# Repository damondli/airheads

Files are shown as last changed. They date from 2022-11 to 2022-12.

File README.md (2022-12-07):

#  ME507 Airheads Glider Project

<div class="title_screenshot">

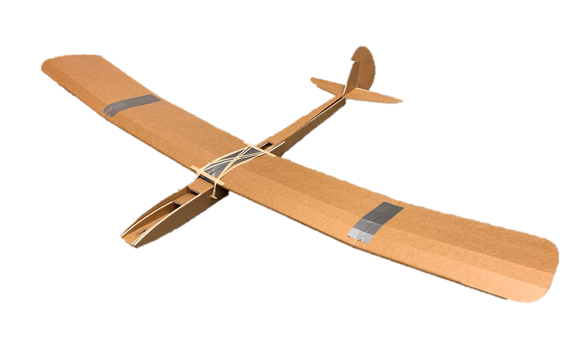
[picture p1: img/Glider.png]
Figure 1. Glider


</div>

This repository documents the development of a flight stabilization system for a glider.
To access our written report for this project, click [here](Airheads_Term_Project_Report_ME507.pdf).

## Background

This is a term project for Cal Poly's ME507 class. The scope of our project consists of:

- Background/Research and Identifying Specifications
- Hardware Design
- Custom PCB Design
- Software Design
- Internet of Things Implementation
- Proper Documentation 

## Hardware Design

To make this project more challenging and more fitting for ME507, we decided to use micro servo body DC motors instead of servos. To implement some form of feedback for the position of the motors, a motor mount was designed to couple a potentiometer to the shaft of the motor.

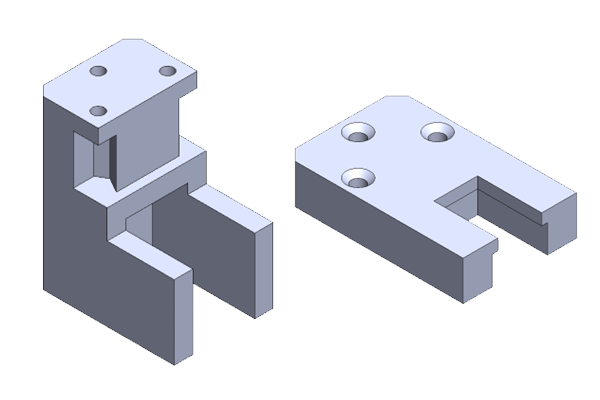
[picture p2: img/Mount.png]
Figure 2. Custom Motor Bracket


## Custom PCB Design

Our custom PCB is designed to fit on an ESP32 feather board.

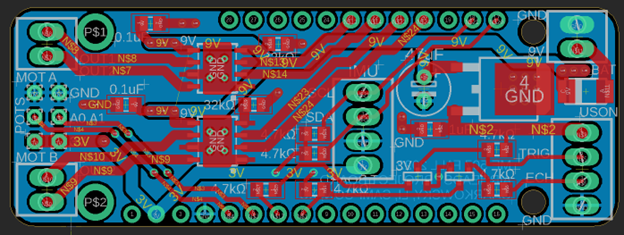
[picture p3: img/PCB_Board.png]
Figure 3. Custom PCB Design


The board supports:
- Two DRV8871 Motor Driver Chips
- Two Potentiometers
- One HC-SR04 Ultrasonic Sensor
- One LIS3MDL + LSM6DSOX IMU Breakout Board

## Software Design

The software includes the following tasks:
- PID Flight Controller
- Ultrasonic Sensor
- Elevator Motor
- Rudder Motor
- Webserver
- IMU

The tasks are organized as shown below in the task diagram.

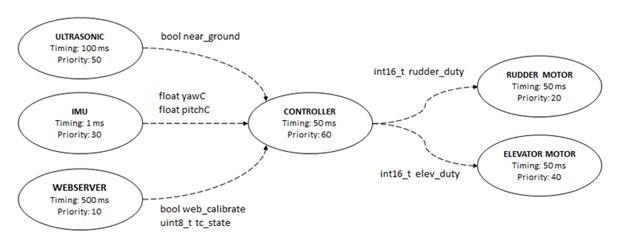
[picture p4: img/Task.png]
Figure 4. Task Diagram


Our controller task is structured as a finite state machine with three states.

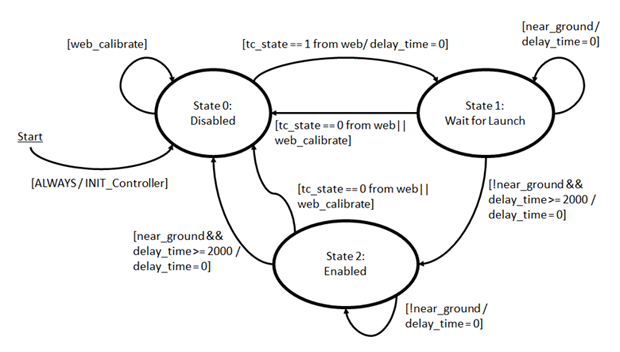
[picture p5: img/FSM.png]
Figure 5. Finite State Machine


Every task runs "simultaneously" though cooperative multitasking with FreeRTOS.

## Internet of Things (IoT)

To implement the IoT, the ESP32's Wi-Fi module is used to host webpage where the user can interact with the flight control system.

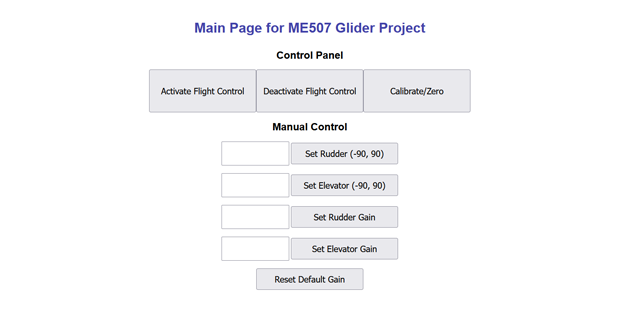
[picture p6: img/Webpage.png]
Figure 6. Webpage Control Panel


Through the webpage, we have the capability to activate, deactivate, and calibrate the flight control system. With more time, we would like to enable our program to support GET or POST requests to accept the user's typed input. This way we can seamlessly update our PID gains without recompiling and uploading our program for each iteration. 

## Documentation and Report

For full documentation of our code, please visit [here](https://damondli.github.io/airheads/).
Our written report for this project can be accessed [here](Airheads_Term_Project_Report_ME507.pdf).

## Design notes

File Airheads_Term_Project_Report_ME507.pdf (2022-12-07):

# Automatic Flight Control and Landing of a Model Glider

## Shea Charkowsky, Damond Li, Arielle Sampson, Daniel Xu

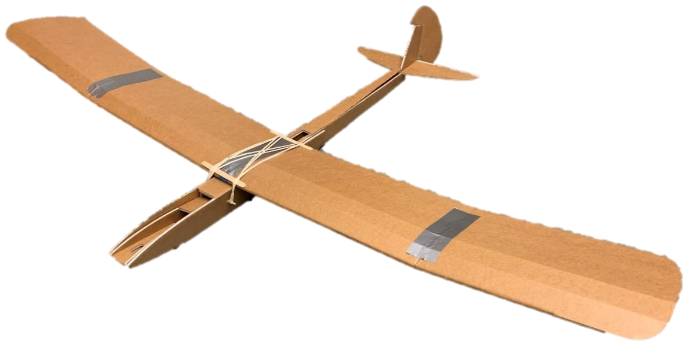
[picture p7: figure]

### ME 507: Mechanical Control System Design

### Professor John Ridgely

### Department of Mechanical Engineering, Cal Poly, San Luis Obispo

Fall 2022

Full Documentation:

https://damondli.github.io/airheads/index.html

Source Code Repository:

https://github.com/damondli/airheads

## I. Index

## a. List of Figures

## II. Introduction

One of the main causes of accidents in small general aviation airplanes is pilot error on takeoff and

landing. While taking off and landing, it is easy for the pilot to stall the airplane because of slow

speeds and high angles of attack. With stall situations, it is also common for general aviation

airplanes to experience spin, which is a yaw-aggravated stall that results in rotation about the spin

axis. Without significant practice, stalls and spins can lead to deadly accidents.

For this project, we focused on controlling the landing of a model glider. The model glider

represents a small, general aviation airplane that has lost engine power and must perform a power-

off landing. Power-off landings are particularly dangerous because the pilot has no option to abort

the landing or perform a touch-and-go landing, which is a form of aborted landing after a

touchdown. So, the control system described in this report is designed to automatically control the

unpowered landing of a model glider. This project represents a proof-of-concept for an automated

landing system that will theoretically take over from a pilot if they encounter a dangerous situation

during landing. The control system is designed to maintain steady flight through descent and then

commands a landing configuration with a slight positive pitch to safely land the aircraft.

This control system is designed for use especially by inexperienced pilots who may encounter

dangerous stall or spin situations without the expertise to quickly correct the problem. While it

would be most useful for new pilots, it could also be implemented into all general aviation

airplanes as an added safety measure. Especially on takeoff and landing, it is critical that the

airplane does not stall or spin because there is not enough altitude to recover from the mistake.

This control system could prevent and correct pilot errors leading to these dangerous situations.

The following report discusses the specifications, development, and results of the hardware and

software for this stabilization system.

## III. Specifications

This flight control system is designed to prevent stall and spin situations in small airplanes during

unpowered landings. The system will be integrated into a model glider to demonstrate its

performance. The system has several testable specifications, each of which has a pass or fail

criterion. The flight control system must meet the requirements listed in Table 1 below.

Table 1: Specifications for Flight Control System

ID | Requirement | Verification Method | Rationale
1. The system shall measure the | aircraft’s distance to the ground with 10 cm accuracy. | Demonstration | The system must recognize when the aircraft is close to the ground so that the landing configuration can be established.
2. The system shall measure the | aircraft’s roll, pitch, and yaw angles with 1-degree accuracy. | Demonstration | The system must identify the attitude of the aircraft to prevent stalls and spins during the flight.
3. The system shall actuate a | rudder control surface between -35 and 35 degrees. | Demonstration | The system must be able to respond to dangerous yaw angles to prevent spins during flight.
4. The system shall actuate an | elevator control surface between -30 and 17 degrees. | Demonstration | The system must be able to respond to dangerous pitch angles to prevent stalls during flight.
5. The system shall communicate | the aircraft’s vertical position and attitude via an HTML webpage. | Demonstration | The system must communicate with a remote user so the user can verify the status of the aircraft.
6. The system shall fit inside the | fuselage of a Flite Test Simple Soarer glider (2” x 2” x 12”) [1]. | Inspection | The system will be demonstrated using a model glider body for proof-of-concept.
7. The system shall weigh less than | 100 grams. | Inspection | The aircraft used to test the system will be a model glider that can have a payload of up to 100 grams.

Each of these specifications for the automatic flight control system will be validated during the

project according to the listed validation method.

## IV. Design Development

Initially, we considered designing a flight control system for automated takeoff and landing but

realized that there may be issues with flying powered remotely controlled airplanes on Cal Poly’s

campus. So, we “landed” on a glider design that would be capable of demonstrating an automated

landing system. Using a glider without a propulsion system, the flight control system demonstrates

the ability to prevent stall or spin situations on landing. During takeoff and landing, the airplane is

relatively close to the ground, so there is little time that can be used to recover from a stall or spin.

Especially in an engine-out landing scenario, the airplane flies at very low speeds, so it is easy for

a pilot to inadvertently stall the aircraft. It is important for the airplane not to pitch up too far on

landing, which could stall the airplane. Additionally, if the airplane stalls with a yaw component,

a spin may occur. Spins are especially difficult for inexperienced pilots to recover from in general

aviation airplanes. So, the flight control system discussed in this report will prevent stall and spin

situations during unpowered landings.

The system will be integrated into a model glider to demonstrate the control of the elevator and

rudder control surfaces during unpowered flight. The flight control system will prevent the airplane

from pitching up and yawing during landing. The system will use an IMU in the fuselage of the

airplane to detect orientation and acceleration in the pitch and yaw axes. Using the information

from the IMU, the system will automatically move the rudder and elevator of the model glider to

prevent high angles of attack with yaw components. The system will also include an ultrasonic

sensor that will be used to detect when the glider is approaching the ground. The ultrasonic sensor

will detect when the glider has landed, and the system will automatically power off to prevent any

damage or additional movement of the control surfaces while on the ground. This is a proof-of-

concept system that could be further developed for use in general aviation airplanes.

## a. Hardware Design

### Hardware Parts

The objectives of the project which involved hardware included (a) detection of plane orientation,

(b) movement of rudder and elevator, and (c) launch and landing detection. Orientation was

measured with a small IMU on a breakout board purchased from Adafruit. Control surface

movement was performed with a DC motor in a servo body mounted to the fuselage. A

potentiometer was coupled to the DC motor to detect the orientation of the motor shaft. Launch

and landing was determined by the distance below the plane measured by an ultrasonic sensor.

These parts were integrated with an ESP32 Feather attached to a custom PCB and powered by a

9V source. A list of major hardware components used is provided in Table 2. Components such as

voltage regulators, resistors, and capacitors were also used in the design of this system but are not

included in Table 2 for clarity.

Table 2: Major Hardware Components Used

Part | Quantity | Rationale
ESP32 Feather Board | 1 | Lighter and smaller than normal ESP32
HC-SR04 Ultrasonic Sensor | 1 | Detect distance from ground
DC Motor in Micro Servo Body | 2 | Control rudder and elevator
Potentiometer | 2 | Attach to DC motor for control surface movement
3.7V 450mAh Li-Polymer Battery | 1 | Small, light battery with enough voltage to power all system components
LSM6DSOX 6-DoF IMU | 1 | Accelerometer and gyro to tell direction and speed
DRV8871 Motor Driver Chip | 2 | Motor driver chip to control DC motors

### Board Design

The PCB was designed to be as small as feasible to fit into the glider fuselage, approximately 3

inches long and 1 inch wide, with screw terminals extending upward and downward about half an

inch each. The circuitry was laid out on an extended shield fit for the pins of the ESP32 Feather.

Our initial schematic and board layout appear in Figure 1 and Figure 2. The board can be divided

into five sections:

1. Power. This section includes a 2-pin screw terminal block for a 9V power source, a

Schottky diode for protection, two capacitors for filtering, and a voltage regulator to shift

down to 5V power for some components.

2. Motors. This section contains two copies of the same circuit, each of which contains a 2-

pin screw terminal, a DRV8871 motor driver chip, a small capacitor for filtering, and a

current-limiting resistor. In the diagram the capacitor and resistor are 0.1 μF and 32kΩ

respectively; due to availability of parts, these were replaced with 1 μF and 33kΩ

components. This circuit receives 9V power.

3. Potentiometers. This section contains through-holes for header pins and traces to 3.3V

power from the Feather and to microcontroller input pin locations.

4. IMU. This section contains a 4-pin screw terminal and two pull-up resistors for I2C data.

It is connected to 3.3V power. The 4.7kΩ resistors of the design were replaced with 3.3kΩ

resistors due to availability.

5. Ultrasonic sensor. This section includes a 4-pin screw terminal and two level-shifting

circuits, each containing two resistors and an N-channel MOSFET. Like for the IMU,

4.7kΩ resistors were replaced with 3.3kΩ resistors.

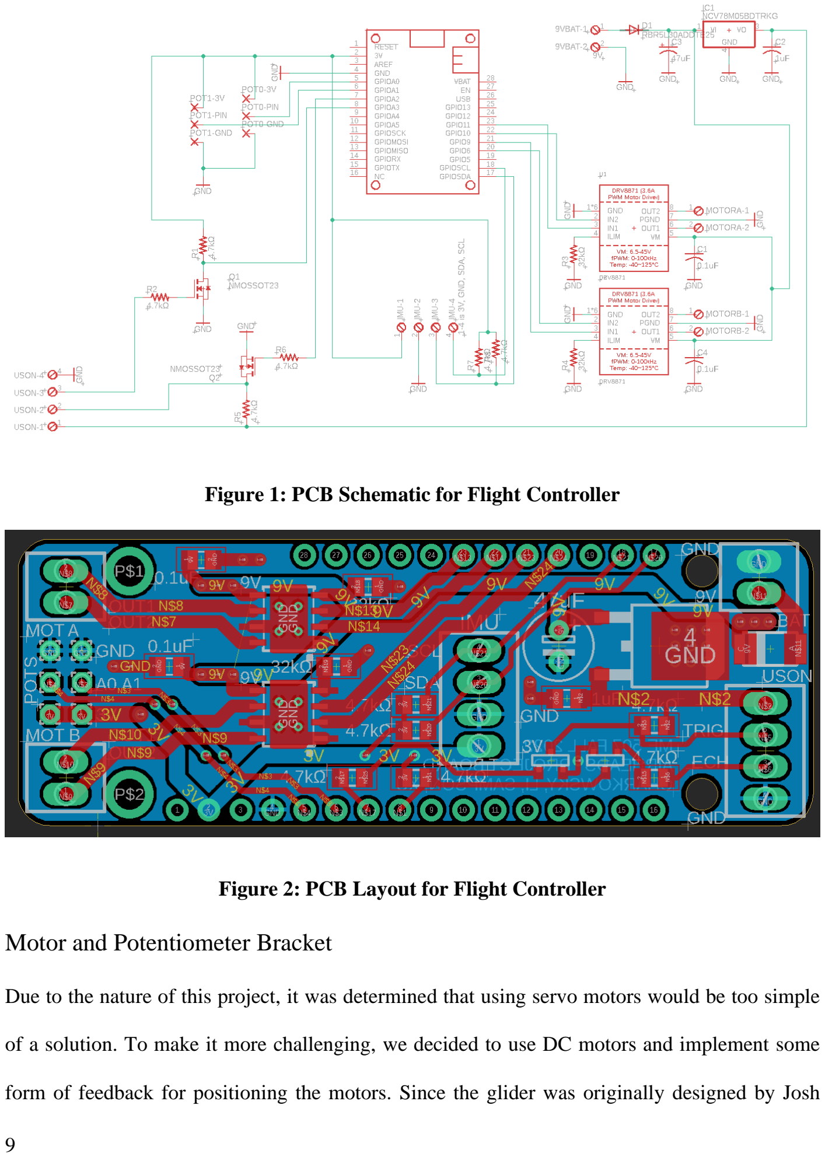
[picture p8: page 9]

Figure 1: PCB Schematic for Flight Controller

Figure 2: PCB Layout for Flight Controller

### Motor and Potentiometer Bracket

Due to the nature of this project, it was determined that using servo motors would be too simple

of a solution. To make it more challenging, we decided to use DC motors and implement some

form of feedback for positioning the motors. Since the glider was originally designed by Josh

Bixler to use small body servo motors, we went with micro servo body DC motors [1]. To

implement some form of feedback, we decided to couple the motor shaft to a potentiometer. The

idea for this was inspired by haptic gloves for virtual reality developed by Lucas De Bonet [2].

A mounting bracket was designed to fit a micro servo body and position a potentiometer directly

above the motor shaft. The initial mounting bracket concept is shown in Figure 3 below.

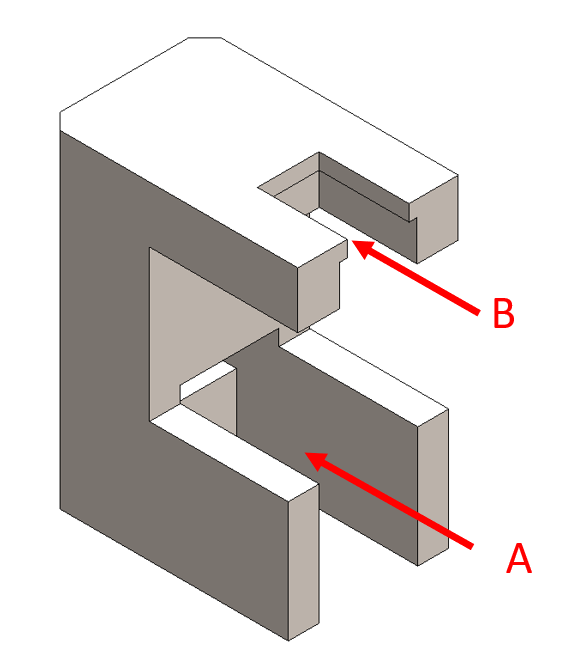
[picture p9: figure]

Figure 3: Micro Servo and Potentiometer Mounting Bracket

The region marked as A is the pocket which the micro servo body fits into. B marks the pocket

where the potentiometer will fit in. There is a little lip at B which constrains the potentiometer

vertically without getting in the way of the terminals. The potentiometer base is also rectangular,

so the parallel pocket will prevent it from rotating. With the motor body and the potentiometer in

position, an adapter is needed to couple the two together. A cross shaped micro servo horn was

chosen for the motor shaft because its geometry would make coupling the two much simpler.

Conveniently, the potentiometer has a slot on the knob which we could use to our advantage. An adapter was designed with the slot and servo cross horn in mind. A three-dimensional drawing of

the DC motor-to-potentiometer coupling knob is shown in Figure 4 below.

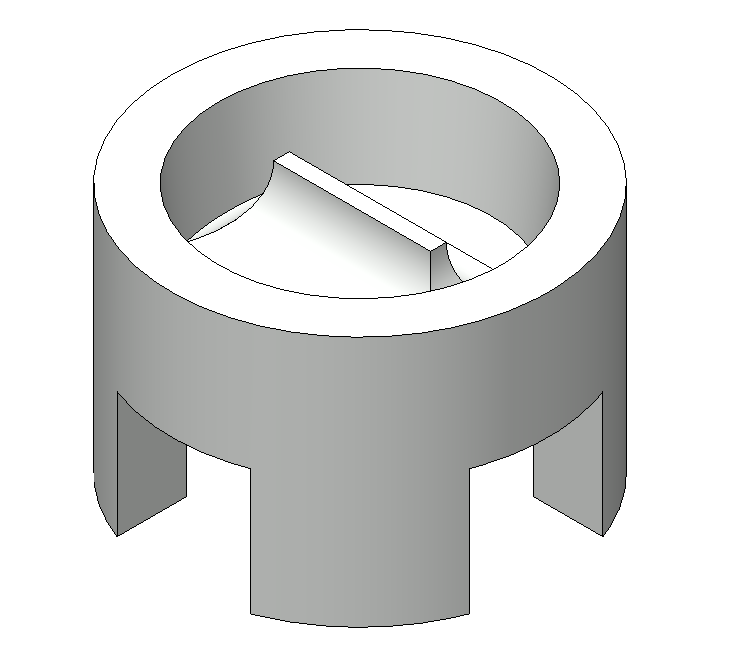
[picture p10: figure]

Figure 4: DC Motor-Potentiometer Coupling Adapter

The four legs would fit between the servo cross horn and the top has a slot that fits into the

potentiometer. The slot is generously filleted to provide structure. The parts were designed with

3D printing in mind as the geometry is rather complex and several iterations are likely needed to

ensure the parts fit nicely together. The complete assembly is shown in Figure 5 below.

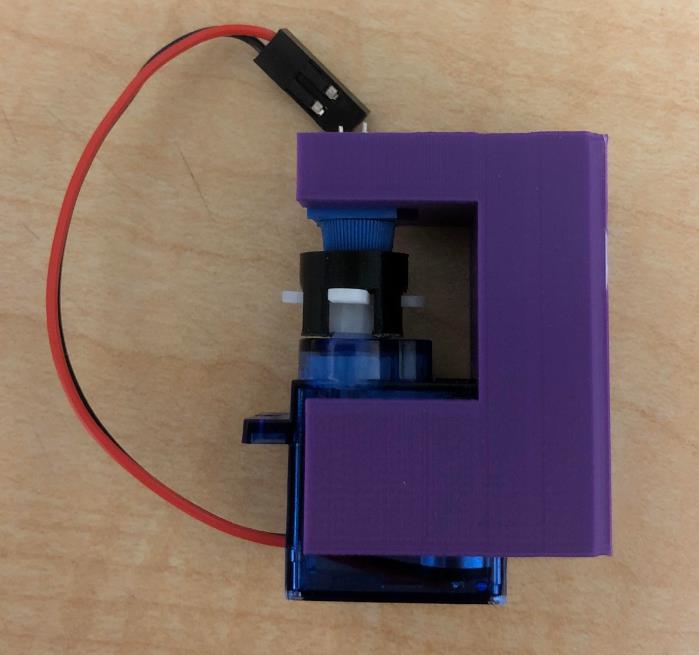
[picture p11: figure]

Figure 5: Complete DC Motor and Potentiometer Mounting Assembly

One issue we noticed with this design is that assembly is easy, but disassembly was difficult. The

parts are so well constrained that both the motor and potentiometer need to be pulled out at the

same time or you risk breaking the thin and fragile tab on the adapter. The simplest solution would

be to split the part in half which is what we did. Our final design for the DC motor-to-potentiometer

mounting assembly is shown in Figure 6 below.

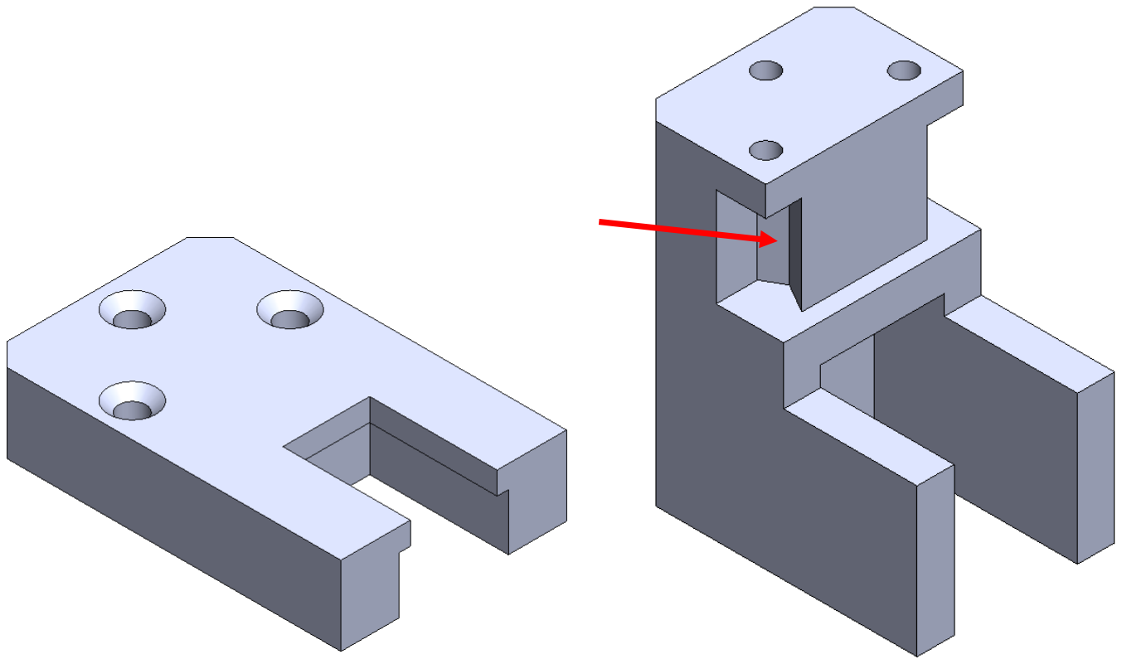
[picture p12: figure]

Figure 6: Redesigned DC Motor and Potentiometer Mounting Bracket

The cap and the base are held together with M2 countersunk screws. The pocket indicated by the

arrow fits an M2 nut and allows us to tighten the screws without fitting a socket or wrench which

would be extremely difficult given the size and geometry of the part. There is also a similar pocket

for the screw in the back (not shown). For the complete set of engineering drawings, please refer

to Appendix B.

## b. Software Design

The software implemented for this flight control system consists of four drivers (motor, inertial

measurement unit (IMU), potentiometer, and ultrasonic sensor), a PID controller class, a module

for a webpage through the ESP32’s Wi-Fi, and a main script to run everything. Other source files

such as the baseshare, taskshare, and printstream modules provided by Dr. John Ridgely were also

utilized during the development of this project [3][4].

### Motor Driver

The motor driver was modified from a script that changes the brightness of an LED which is

originally written by Rui and Sara Santos [5]. The modified script was then converted into a class

which allows the user to specify the pins and channels they want to use. A snippet of code from

the DRV8871 motor driver class constructor is shown in Figure 7 below.

/** @brief | Constructor for the DRV8871 motor driver class
* @param | pin_A The GPIO pin from the ESP32 (non-zero PWM for a positive
* | duty cycle)
* @param | pin_B The GPIO pin from the ESP32 (non-zero PWM for a negative
* | duty cycle)
* @param | channel_A The timing channel for pin_A
* @param | channel_B The timing channel for pin_B
*/
DRV8871::DRV8871(uint8_t pin_A, uint8_t pin_B, uint8_t channel_A, uint8_t channel_B)
{
// Establish the output pins
PIN_A = pin_A;
PIN_B = pin_B;

// Establish the channels
CHANNEL_A = channel_A;
CHANNEL_B = channel_B;

// Setup pins with the appropriate resolution and frequency ledcSetup(CHANNEL_A, frequency, resolution); ledcSetup(CHANNEL_B, frequency, resolution);

// Attach the pins to the channel ledcAttachPin(PIN_A, CHANNEL_A); ledcAttachPin(PIN_B, CHANNEL_B); }

Figure 7: DRV8871 Motor Driver Class Constructor

To create a DRV8871 motor object, two pins and two channels need to be specified. The pins

correspond to the GPIO pins, and there are a total of 16 difference channels on an ESP32. Because

we need each pin output its own independent waveform, we made sure to enter a unique channel

for each pin even across multiple instances of the motor class. The frequency refers to the

frequency of the pulse width modulated wave. We used a frequency of 20,000 which is just outside

the limits of human hearing so there is no annoying audible noise when operating our motors. The

resolution refers to the number of bits that will be used to describe the duty cycle. We set our resolution to 8, meaning that to get a 100% duty cycle we need to set the pin channel to a value of

255. The method that is used to set various duty cycles is shown in Figure 8 below.
/** @brief | Outputs the desired PWM signal to the appropriate output pin given
* | a duty cycle
* @param | duty_cycle The duty cycle to run the motors
*/
void DRV8871::set_duty(int16_t duty_cycle)
{
// Check max and min boundaries for duty cycle inputs if (duty_cycle > 100)
{
duty = 100;
}
else if (duty_cycle < -100) {
duty = -100;
}
else
{
duty = duty_cycle;
}

// Scale the duty cycle according to the resolution of the channel duty = duty * max_duty / 100;

// Check to see which channel to use given the signage of the duty cycle
if (duty > 0) | // Use Channel A
{
ledcWrite(CHANNEL_A, duty);
ledcWrite(CHANNEL_B, 0);
}
else if (duty < 0) | // Use Channel B
{
ledcWrite(CHANNEL_B, (-1 * duty));
ledcWrite(CHANNEL_A, 0);
}
else | // Both channels set to zero duty cycle
{
ledcWrite(CHANNEL_A, 0);
ledcWrite(CHANNEL_B, 0);
}
}

Figure 8: Method to Set Various Duty Cycles

The set_duty method first checks if the input argument exceeds the upper or lower bound of 100

or -100, respectively. The input duty cycle is then scaled to the maximum value which is

determined by the resolution of the channel (255 for an 8-bit resolution channel). Depending on

the sign of the input duty cycle, the channels will be set accordingly. CHANNEL_A will be non-

zero and CHANNEL_B will be zero for positive duty cycles and vice versa for negative duty

cycles. Note that the ledcWrite function only accepts positive values, so the duty is multiplied by

negative one before calling the ledcWrite function for negative duty cycles.

### IMU Driver

The IMU driver is used to find the yaw, pitch, and roll and is composed of two different chips. The

LSM6DSOX chip is responsible for interfacing with the accelerometer and the gyroscope. The

LIS3MDL chip is responsible for interfacing with the magnetometer. Both chips use I2C to

communicate with the MCU, of which, we integrated the Adafruit public libraries to do so. The

most important feature of our IMU driver class is to combine magnetometer, accelerometer, and

gyroscope measurements to get the measurements we want, which we did so through the get_angle

method. This is done by first reading the raw data for the different sensors. Using accelerometer

measurements, the angles φ and ψ are calculated using equations 1 and 2 below.

### φ = tan⁻1

(

AccelX
AccelY

2+AccelZ

2) Equation 1

### ψ = tan⁻1

(

AccelY
AccelX

2+AccelZ

2) Equation 2

The code implementation of this equation is shown in Figure 9. It is uneccessary to calculate θ

using this method because the accelerometer uses gravitational forces. Since θ uses the downward

force, changes in measurements can not be evaluated, therefore yaw can not be determined. The code implementing the φ and ψ angles in the get_angle method is shown in Figure 9 below. The

term that is zeroed out is an integration term based on gyroscope movement, which we ignored

because it caused unpredictable fluctuations in measured angles.

// read data values for gyro and accelerometer read_data(GyroX, GyroY, GyroZ, AccelX, AccelY, AccelZ);

// calculate phi and psi for pitch and roll
// phi is used to determine pitch
// psi is used to determine roll
phi = atan2(AccelX,(sqrt(AccelY*AccelY + AccelZ*AccelZ))); psi = atan2(AccelY,(sqrt(AccelX*AccelX + AccelZ*AccelZ)));

// Calculate pitch and roll
// Equations for both integration of gyroscope with accelerometer // and equations that do not use gyroscope

// equations with gyro integration
// pitch_in = 0.98*(pitch + GyroX*dt) + 0.02*phi - pitch_offset; // roll_in = 0.98*(roll + GyroY*dt) + 0.02*psi - roll_offset;

// equations without gyro integration
pitch_in = round((0.00*(pitch + GyroX*dt) + 1.00*phi - pitch_offset) * 180/M_PI) * M_PI/180;
roll_in = round((0.00*(roll + GyroY*dt) + 1.00*psi - roll_offset) * 180/M_PI) * M_PI/180;

Figure 9: Implementation of φ and ψ code in the get_angle method.

φ and ψ are variables used to calculate pitch and roll angles. Pitch and roll calculations can be

done with the implementation gyroscope measurements alongside accelerometer measurements,

however, due to gyroscope drift and other inaccuracies relating to the sensor, we decided to use

only the accelerometer. Additionally, we used a roll and pitch offset to account for the initial

measurement errors for when the IMU is flat.

To calculate yaw, the magnetometer data is needed. The magnetometer measures the strength and

direction of the magnetic field. This data can be used in conjunction with the pitch and roll

calculations to find yaw. A snippet of the code used for this method is shown in Figure 10.

// Calculates new Magnetometer angles with tilt compensations
nMAGX = MAGX*cos(pitch) + MAGZ*sin(pitch);
nMAGY = MAGX*sin(roll) * sin(pitch) + MAGZ*sin(roll)*cos(pitch);

// calculates yaw using new magnetometer readings
yaw_in = atan2(-nMAGY,nMAGX) - yaw_offset;

// sets pitch, roll, and yaw to be stored for future use pitch = pitch_in;
roll = roll_in;
yaw = yaw_in;

Figure 10: Determining Yaw

First, using the pitch and roll calculations, new magnetic field measurements for the X and Y

directions can be calculated. This allows for effects of tilt to be accounted for so that X and Y

readings can be accurate, even when the IMU is not parallel to the ground. Yaw can then be

calculated from the adjusted magnetometer readings. A yaw offset is used so the initial direction

that the plane is facing can be set to 0 degrees. In an ideal scenario, the magnetometer would only

have to measure the Earth’s magnetic field. However, due to the many large metal objects in the

vicinity of the lab space that distorted the magnetic field, its measurements were not reliable. While

we were not able to find a method to account for these distortions, an actual implementation of the

glider flying outside would not encounter these problems.

### Potentiometer Driver

The potentiometer driver is rather simple. The voltage will be measured from a specified GPIO

pin and converted into an angle value [degrees]. The conversion between voltage to degrees was

determined experimentally. A snipped of code from the potentiometer driver class that shows

methods for zeroing and getting the position of the potentiometer is shown in Figure 11 below.

/** @brief Measures position of the potentiometer
* @returns The position of the potentiometer in units of degrees
*/
float Potentiometer::get_angle(void)
{
// Default resolution is 12 bits. Outputs 0 - 4096 adc_value = analogRead(ADC_PIN);

// Convert the ADC values to a voltage
voltage = VOLTAGE_SOURCE * adc_value / ADC_RANGE;

// Offset the voltage reading and convert to degrees
float angle = (voltage - voltage_offset) * VOLTAGE_TO_DEGREES;

return angle;
}

/** @brief Zeros the position of the potentiometer by setting the offset voltage
* | to the voltage measured at its current position
*/
void Potentiometer::zero(void)
{
// Assuming the potentiometer is positioned at the zero // Get current voltage reading
float current_voltage = get_voltage();

// Set the offset to the current voltage voltage_offset = current_voltage;
}

Figure 11: Method for Zeroing and Getting Position of Potentiometer

In the get_angle method, the voltage is read from ADC_PIN, and scaled appropriately with

VOLTAGE_SOURCE and ADC_RANGE which converts the ADC reading to a value between 0-

3.3V. The angle is then calculated by multiplying the difference between the current voltage and

voltage_offset by a constant called VOLTAGE_TO_DEGREES. It is important to note that the

relationship between voltage and its angular position is not linear. Rotating the potentiometer 90

degrees in one direction may output a value of 90 degrees but rotating 90 degrees in the other

direction from center may output a value of about 140 degrees. The potentiometer also tends to

saturate well before reaching its rotational limit. In other words, there is only a small region where

the output voltage changes with position and anything beyond that will either read as 0V or 3.3V.

### Ultrasonic Sensor Driver

The ultrasonic sensor driver is modified from a script written by Arbi Abdul Jabbaar. We modified

Jabbaar’s script by converting it into a class. The ultrasonic sensor works by intermittently emitting

ultrasonic pulses and measuring the time that it takes to bounce off an object and back to the sensor.

A snippet of code which shows how the distance is measured is included in Figure 12 below.

/** @brief Measure the distance between the sensor and the object in
* front of it
* @returns The distance, in centimeters, between the sensor and the object in front of it
*/
float ultrasonic::get_distance (void)
{
distance; | // variable to store calculated distance
duration; | // variable for the duration of sound wave travel

// Clears the trigPin condition
digitalWrite(trigPin, LOW);
delayMicroseconds(2);

// Sets the trigPin HIGH (ACTIVE) for 10 microseconds digitalWrite(trigPin, HIGH);
delayMicroseconds(10);
digitalWrite(trigPin, LOW);

// Reads the echoPin, returns the sound wave travel time in microseconds duration = pulseIn(echoPin, HIGH);

// Calculating the distance
distance = duration * 0.034 / 2; // Speed of sound wave divided by 2 (go and back)

return distance; // return distance measurement in cm
}

Figure 12: Distance Calculation from Ultrasonic Sensor

The trigger pin (trigPin) is set to high for ten microseconds which emits the ultrasonic pulses. The

pulseIn function is then used to determine the time it takes for the pulse to bounce off the object

and back to the sensor. The 0.034 value is from the 340 m/s speed of sound, and the division by

two is from the fact that the pulse will have traveled twice the distance between the sensor and the

object before it is received.

### Network Module

To host our own webpage from our ESP32, we used a module provided by Dr. John Ridgely which

is based on an example by A. Sinha. One drastic modification that we have made to this module

is by implementing R”rawliteral()rawliteral”. The HTML header from the original code is shown

in Figure 13 below.

a_string += "<!DOCTYPE html> <html>\n";
a_string += "<head><meta name=\"viewport\" content=\"width=device-width,"; a_string += " initial-scale=1.0, user-scalable=no\">\n<title> ";
a_string += page_title;
a_string += "</title>\n";
a_string += "<style>html { font-family: Helvetica; display: inline-block;"; a_string += " margin: 0px auto; text-align: center;}\n";
a_string += "body{margin-top: 50px;} h1 {color: #4444AA;margin: 50px auto 30px;}\n";
a_string += "p {font-size: 24px;color: #222222;margin-bottom: 10px;}\n"; a_string += "</style>\n</head>\n";

Figure 13: Original Code for HTML Network Header

This is essentially trying to squeeze HTML code into one string which makes it difficult to read

and debug if needed, especially with “\” and “\n” scattered throughout. By implementing

R”rawliteral()rawliteral”, the same piece of code is rewritten in Figure 14 below.

a_string += R"rawliteral(
<!DOCTYPE html>
<html lang="en">
<head>
<meta charset="utf-8">
<meta name="viewport" content="initial-scale=1, width=device-width">
<title>)rawliteral";
a_string += page_title;
a_string += R"rawliteral(
</title>
<style>
html { font-family: Helvetica; display: inline-block; margin: 0px auto; text-align:center;}
body { margin-top: 50px;}
h1 { color: #4444AA; margin:50px auto 30px;}
p { font-size: 24px; color: #222222; margin-bottom:10px;} input { width:250px;height:100px;font-size:20px;} </style>
</head>
)rawliteral";

Figure 14: Rewritten HTML Header Code

Although it is not as compact as the original code, we are able to retain the HTML format where

the beginning and end of each tag are indented and aligned appropriately. This change is more

apparent when writing the body portion of our webpage, shown in Figure 15 below.

a_str += R"rawliteral(
<body>
<main>
<div id="webpage">
<h1>Main Page for ME507 Glider Project</h1> <h2>Control Panel</h2>
<table>
<tr>
<form action="/activate">
<input type="submit" value="Activate Flight Control">
</form>
<form action="/deactivate">
<input type="submit" value="Deactivate Flight Control">
</form>
<form action="/calibrate">
<input type="submit" value="Calibrate/Zero"> </form>
</tr>
</table>
<h2>
Manual Control
</h2>
<form action="/set_rudder">
<input type="text" style="width:150px;height:50px;font-size:20px;">
<input type="submit" value="Set Rudder (-90, 90)" style="width:250x;height:50px;font-size:20px;"> </form>
<br>
<form action="/set_elevator">
<input type="text" style="width:150px;height:50px;font-size:20px;">
<input type="submit" value="Set Elevator (-90, 90)" style="width:250x;height:50px;font-size:20px;"> </form>
<br>
<form action="/">
<input type="text" style="width:150px;height:50px;font-size:20px;">
<input type="submit" value="Set Rudder Gain" style="width:250x;height:50px;font-size:20px;"> </form>
<br>
<form action="/">
<input type="text" style="width:150px;height:50px;font-size:20px;">
<input type="submit" value="Set Elevator Gain" style="width:250x;height:50px;font-size:20px;"> </form>
<br>
<form action="/">
<input type="submit" value="Reset Default Gain" style="width:250x;height:50px;font-size:20px;"> </form>
</div>
</main>
</body>
</html>
)rawliteral";

Figure 15: HTML Webpage Body

Our webpage consists of three main buttons: one to activate the flight control, one to deactivate

the flight control, and one to zero the potentiometers on the glider. When the buttons are pressed,

the user is redirected to their respective HTML page: “/activate”, “/deactivate”, and “/calibrate”.

The code to handle the “/activate” HTML page is shown in Figure 16 below.

/** @brief Switches the state in a FSM when called by the web server.
* @details This method alters a shared variable that contains the current state
* | of a FSM in the controller task located in main.cpp. The state is
* | switched to 1.
*/
void handle_Activate (void)
{
tc_state.put(1);

String toggle_page = "<!DOCTYPE html> <html> <head>\n";
toggle_page += "<meta http-equiv=\"refresh\" content=\"1; url='/'\" />\n"; toggle_page += "</head> <body> <p> <a href='/'>Back to main page</a></p>"; toggle_page += "</body> </html>";

server.send (200, "text/html", toggle_page);
}

Figure 16: Code for “Activate” Button on HTML Webpage.

When the user is sent to “/activate”, the page refreshes and redirects the user back to “/”. The code

shown does not follow the R”rawliteral()rawliteral” formatting described earlier simply because

little to no change needed to be made as its only purpose is to redirect the user back to “/”.

### PID Controller Class

We decided to use proportional, integral, and derivative (PID) controller for our glider. We

concluded that for our proof-of-concept demonstration, only proportional control was necessary

for this project. However, we did structure our PID controller task so that integral and derivative

control can easily be implemented if we knew the gains. The code for the PID controller class is

shown in Figure 17 below.

/** @brief Initialize PIDController class
*/
PIDController::PIDController(float Kp_in, float Ki_in, float Kd_in, float dt_in) {
Kp = Kp_in;
Ki = Ki_in;
Kd = Kd_in;
dt = dt_in;
errIntegral = 0; | // Reset integral of error
errPrev = 0; | // Reset error at previous time
}

/** @brief Set gains to user-inputted values
*/
void PIDController::setGains(float Kp_in, float Ki_in, float Kd_in) {
Kp = Kp_in;
Ki = Ki_in;
Kd = Kd_in;
}

/** @brief Calculate PID control output at current time
*/
float PIDController::getCtrlOutput(float posCurrent, float posDesired) {
float err = posDesired - posCurrent;
errIntegral += err*dt;
float derr = (err - errPrev) / dt;

return ( Kp*err
+ Ki*errIntegral
+ Kd*derr );

errPrev = err;
}

Figure 17: PID Controller Class

The PID controller includes methods to set and update the proportional, integral, and derivative

gains as well as a method to get the controller output. To run the controller, the current and desired values are first passed in as arguments to the getCtrlOutput method. The difference between the

desired and current value is multiplied by the proportional gain to get the controller output.

## c. Operation of Machine (Tasks and States)

The aircraft system operates using the following six simultaneous tasks:

1. task_ultrasonic, which detects the distance below the plane to the nearest object.
2. task_IMU, which calculates the current attitude of the plane.
3. task_webserver, by which the webpage prompts the user to activate, deactivate, or calibrate

the system.

4. task_controller, which receives the attitude of the plane and the current motor positions

and sends appropriate duty cycles.

5. task_rudder_motor, which receives a duty cycle and outputs corresponding signals to the

rudder motor.

6. task_elevator_motor, which receives a duty cycle and outputs corresponding signals to the

elevator motor.

These tasks exchange shares and are timed and prioritized according to Figure 18 below.

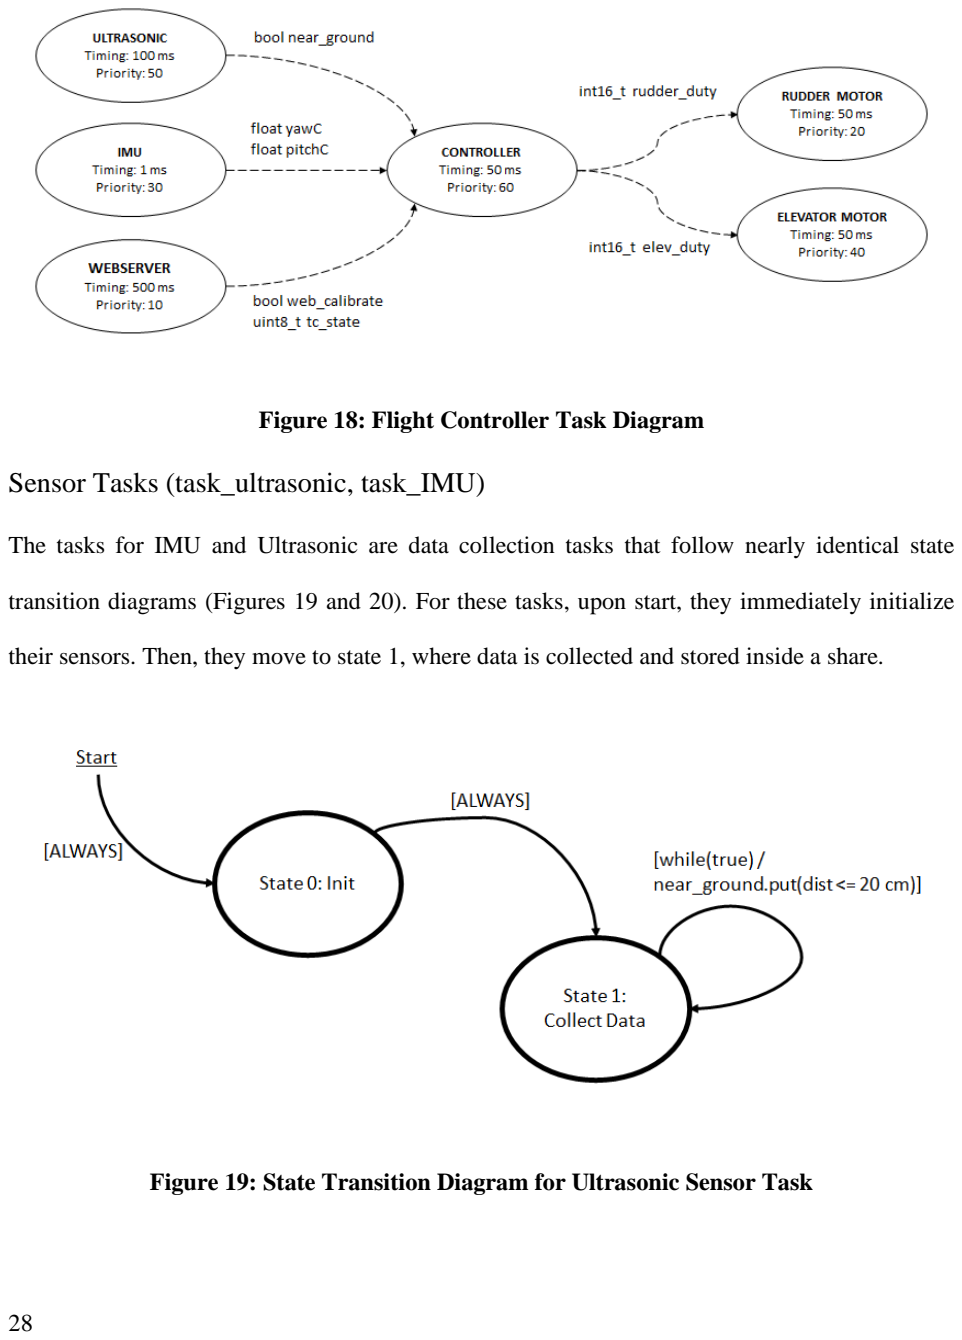
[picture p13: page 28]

Figure 18: Flight Controller Task Diagram

### Sensor Tasks (task_ultrasonic, task_IMU)

The tasks for IMU and Ultrasonic are data collection tasks that follow nearly identical state

transition diagrams (Figures 19 and 20). For these tasks, upon start, they immediately initialize

their sensors. Then, they move to state 1, where data is collected and stored inside a share.

Figure 19: State Transition Diagram for Ultrasonic Sensor Task

The ultrasonic sensor task fetches the detected distance to the nearest object, and then puts to a

share called near_ground whether that distance is below a threshold value, which we set to 20 cm.

This occurs every 100 ms. The share near_ground affects the operation of the controller task.

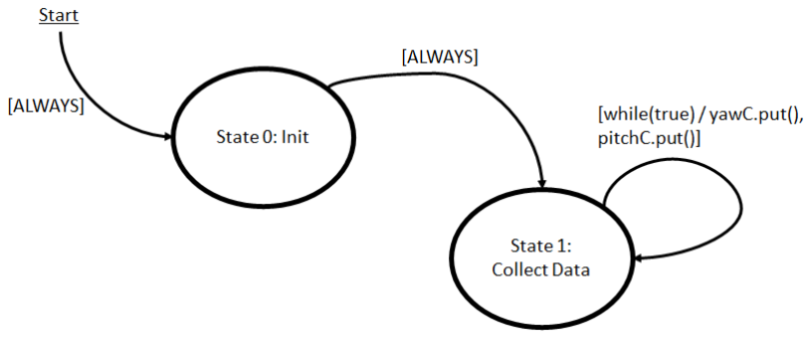
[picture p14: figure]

Figure 20: State Transition Diagram for IMU Task

The IMU task fetches the angle of the IMU and puts those values to shares (yawC and pitchC) for

use by the controller. The task period is very short to avoid drift in integrated values. Angles were

determined based on the direction of gravitational acceleration. For the purposes of the

demonstration, roll angle was used in place of yaw since the indoor environment caused issues

with magnetometer measurements.

### Webserver Task (task_webserver)

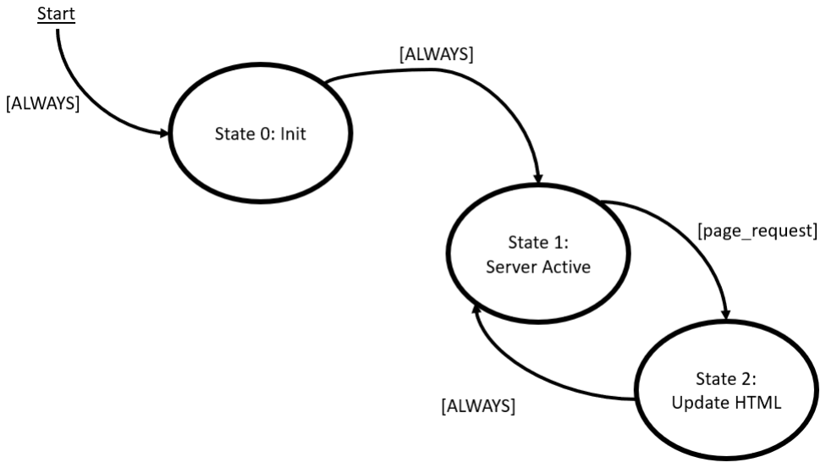
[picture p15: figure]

Figure 21: State Transition Diagram for Webserver Task

The state transition diagram for the web server is shown in Figure 21. When it starts, it always

initializes the server components necessary for it to function. Then, it always goes to state 1, where

the server is active. In state 1, the web server waits for a page update request, then moves onto

state 2, where it updates the HTML. After updating the webpage, the server moves back to waiting

for another page request.

The webserver task provides the user the ability to activate, deactivate, and calibrate or zero the

system. The “Activate” button is necessary to enable the controller. The controller is disabled, and

motor duty cycles are set to zero when the “Deactivate” button is pressed. When the user clicks

the “Calibrate/zero” button, the controller is disabled, the current heading of the plane is set as the

new desired direction, and current position of the control surfaces becomes their new neutral

position.

### Controller Task (task_controller)

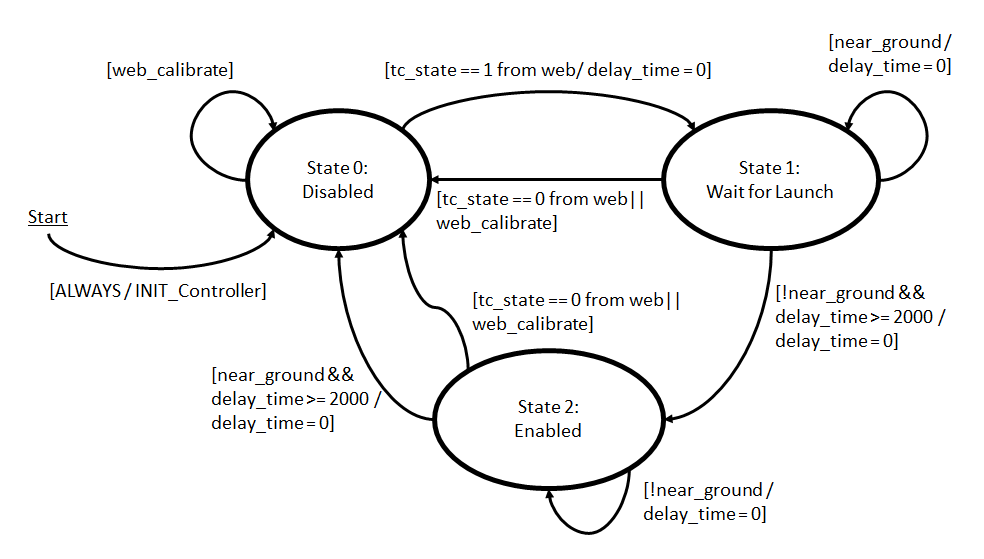
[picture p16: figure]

Figure 22: State Transition Diagram for Controller Task

The state transition diagram for the controller task is shown in Figure 22 above. The controller

task receives current plane angles from the IMU task (via the shares yawC and pitchC), fetches

the current control surface angles from the potentiometers, and outputs motor duty cycles into the

shares called rudder_duty and elev_duty, which are received by the motor tasks.

There are three states in the controller task:

0. Disabled. Motor duty cycles are held at zero. There is no automatic transition into state 1;

this can only be performed by webpage activation through the webserver task.

1. Wait for launch. This delay period is established to prevent unpredictable control surface

movement while the glider is being thrown. Before launch, the user’s hand covers the

ultrasonic sensor so that the sensor reads a very small number, i.e., the share near_ground is set to true by the ultrasonic sensor task. When the user hand-launches the glider, the

ultrasonic detects that the plane is no longer being held (near_ground is false); if this is the

case for two seconds, the controller will move to state 2 and be enabled.

2. Enabled. In this state, the controller will send appropriate duty cycles to the motor tasks.

The overall system requires two layers of control, one for the relationship between plane

attitude and control surface angle, and one for the relationship between the control surface

angle and motor duty cycle. Two layers for each of two systems (rudder and elevator)

resulted in four PID controller objects. In each of these, we only used P control, and gains

were chosen by empirical tuning. When the plane nears landing (i.e., when near_ground is

true), the desired pitch increases to slow the plane. If the plane is near the ground for a

continuous length of time, presumably having landed, the controller moves back to state 0,

disabled.

Within all states, the controller task checks whether the “Deactivate” or “Calibrate/Zero”

commands have been called from the webpage. Both send the controller state to 0. Instead of

including copies of this code in every state, these checks are written at the top of the task loop so

that they are run during each state.

### Motor Tasks (task_rudder_motor and task_elevator_motor)

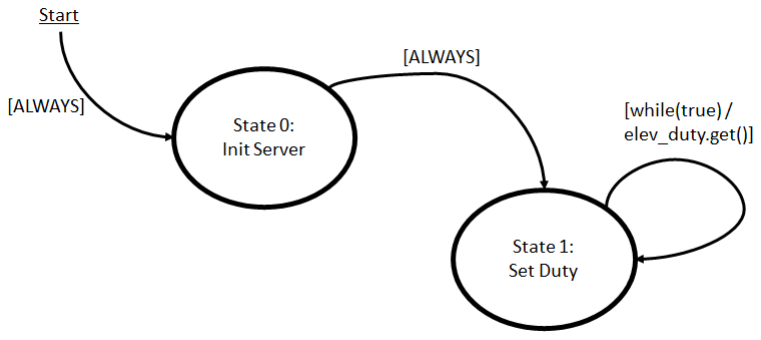
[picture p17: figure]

Figure 23: State Transition Diagram for Elevator Motor Task (task_elevator_motor)

The tasks for both the rudder and elevator motor tasks have functionally identical state transition

diagrams. Figure 23 shows that of the elevator motor; the rudder motor task uses the share

rudder_duty instead of elev_duty. For these tasks, upon start, they immediately initialize the pins

necessary for PWM control. Then, they move to state 1, where they wait until a duty cycle

instruction is received and then set a duty cycle accordingly.

## V. Results

To demonstrate how the flight control system worked, we integrated the system into the model

glider. The system was designed to control the rudder and elevator of the model glider, so we

attached control rods to the two DC motors in micro servo bodies. The control rods were attached

to control horns on the rudder and elevator of the glider. We used a power supply in the lab to

power the system, so we could not demonstrate the glider’s flight as a wireless system. However,

we demonstrated that by moving the IMU attached to a separate breadboard, the rudder and

elevator of the glider automatically moved to counteract the movement of the IMU. The flight

control system behaved as expected during the lab demonstration. If the IMU was placed in the

fuselage of the glider, we could demonstrate that the movement of the glider would directly affect

the movement of the control surfaces.

If we were to continue working on this project, it would be ideal to have the system become

wireless and demonstrate its ability to safely land the glider automatically. We would also include

a landing sequence code that would instruct the control surfaces to push the glider’s nose slightly

up, in more of a realistic landing configuration. The landing sequence would be activated by the

ultrasonic sensor’s measured distance to the ground. Due to the time constraint, we were unable to

implement integral and derivative control to our PID controller. The added resistance from

coupling the potentiometer with the motor increased the stiction in the motor, leading to higher

steady state error. As for the ESP32 hosted webpage, we were able to successfully implement three

buttons: activate, deactivate, and calibrate. With more time, we would like to set it up so that we

can tune each PID gain through the webpage. To do so, we would need to process the user’s input,

likely through a get or post request. We would also need to make sure that the user’s input is valid

(i.e., no letters or no special characters). Although this itself is not too challenging, it requires time which we did not have. Furthermore, with the IMU, there were some additional capabilities that

we did not fully investigate. For example, there was a free-fall detection feature that we could have

implemented. This would have given us a method to detect stalling and add a free-fall recovery

task within the system. Implementing this would have required additional time, calculations, and

testing that would not be possible within the span of this class.

Our in-class demonstration did not use all of our PCB components. While we would have liked to

test and use all five circuits, we chose to reconstruct some circuits using bread boards and breakout

boards to avoid the need to troubleshoot the PCB. The power, potentiometer, and motor circuits

worked in testing, but the ultrasonic sensor circuit did not, and the IMU circuit was left untested.

Of course, all circuits would need to be operational before a true flight test could be possible, and

we would have tested and troubleshot all parts of the PCB if we were in a position in our schedule

to do so.

The biggest improvement that we can make to our glider would be directly measuring the

orientation of the control surfaces rather than the potentiometers coupled to the motor. One idea

we had for this was to couple the potentiometers to the control surfaces instead of the motor. Real

airplanes typically have angle-of-attack sensors on their wings to warn pilots of impending stall.

This system would benefit from having similar sensors on its wings and control surfaces.

Additionally, it would be helpful if our glider had a method to measure air speed. A way to

implement this would be to add a pitot tube to the device. By knowing the airspeed, we would

have more data to work with to assist in stabilizing the glider. However, due to size constraints on

our glider, this would be more applicable for a larger aircraft.

Overall, this project was a great, hands-on learning experience that produced a demonstrable

control system with real-world applications.

## VI. Conclusion

The mechanical control system discussed in this report has the potential to save lives. While its

current form is somewhat simplified as a proof-of-concept system, an automatic stabilization

mechanism for general aviation airplanes is a potentially life-saving system. As seen with the

Boeing 737 MAX crashes in 2019, a faulty automatic stabilization system also has the ability to

end lives. The flight control system developed in this class could positively affect the welfare of

pilots and passengers alike, and the safety of those using this system was a continuous concern. In

general aviation airplanes, this system is designed to prevent dangerous situations for pilots; for

this project, we also considered the safety of those testing the system. For example, we ensured

that once the glider had landed, the control surfaces would stop moving to prevent any damage to

the model or to people in the area.

The flight control system behaved as expected and demonstrated its ability to automatically move

the glider’s elevator and rudder in response to movement of the IMU. Overall, this was a successful

project for The Airheads and a significant learning experience. This project included an embedded

computer, several sensors for measuring operational parameters, a custom circuit board, several

actuators, multitasking software to implement controls, digital communication via Wi-Fi, and

documentation of the control system development process.

Throughout this project, we each gained experience in designing printed circuit boards and

mechanical control systems for real-world applications. Using the skills developed in ME 507, we

selected a problem for which mechatronics was a good solution and performed high-level design

of a mechatronic system. For this project, we designed complex programs using an organized

methodology including task and state diagrams. We designed a printed circuit board for the flight

control system and selected appropriate components at reasonable costs. Throughout the project, we found and utilized design data for system components using resources like data sheets. We

documented hardware and software designs through written documentation and code commenting.

As a team, we effectively worked to develop a flight control system as a solution to a mechatronics

problem.

## VII. Appendix

## a. Source Code and Documentation

Full Documentation: https://damondli.github.io/airheads/index.html

Source Code Repository: https://github.com/damondli/airheads

Dr. John Ridgely’s ME507 Support Files: https://github.com/spluttflob/ME507-Support

## b. Servo Body Mount Design

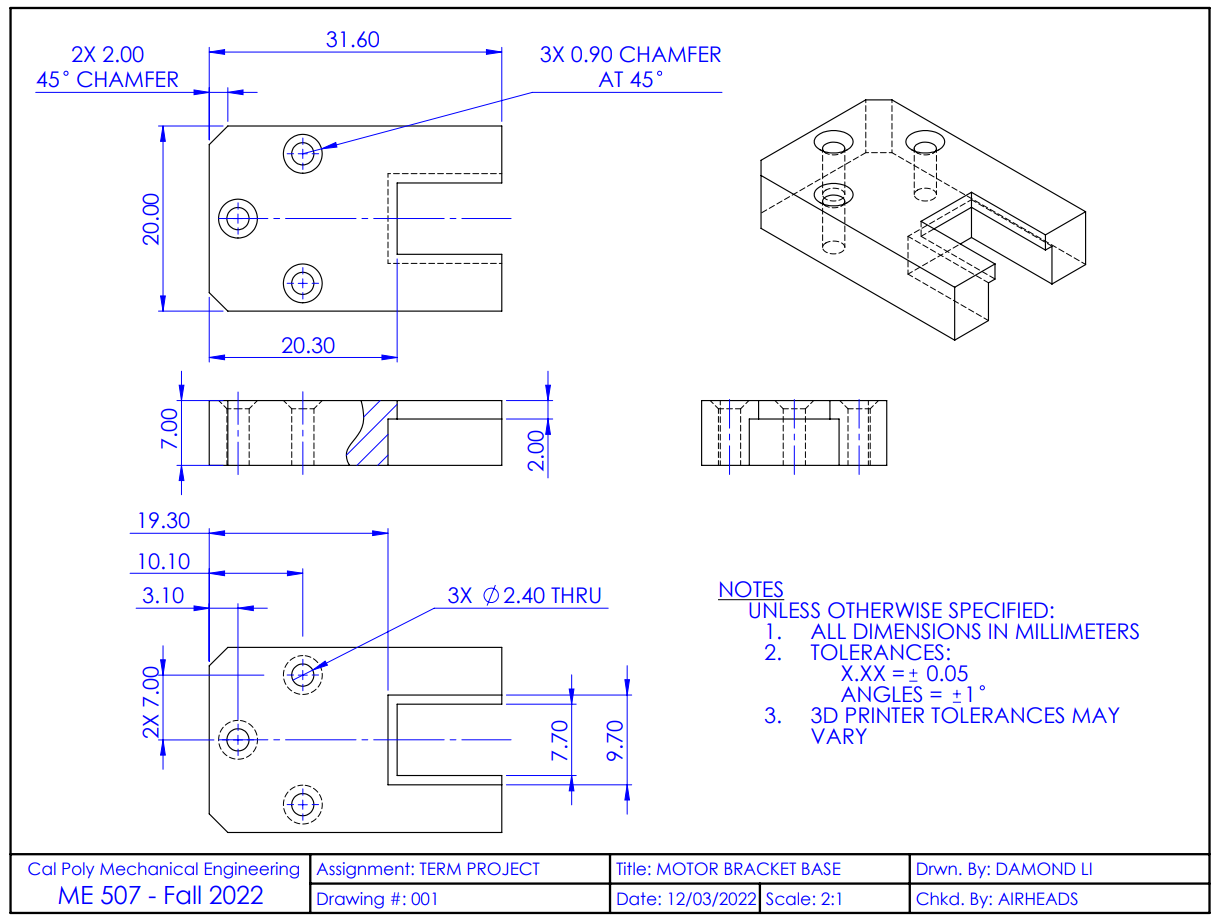
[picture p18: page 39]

39

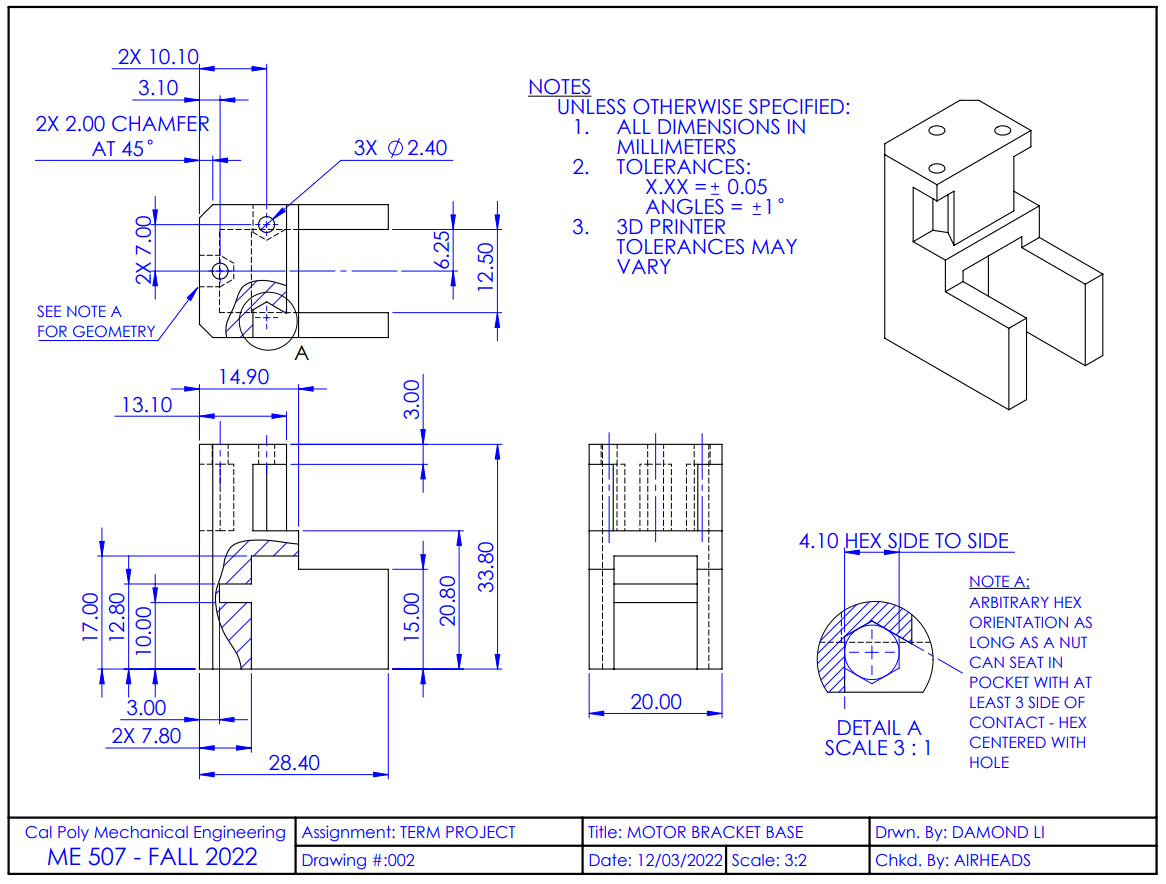
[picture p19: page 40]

40

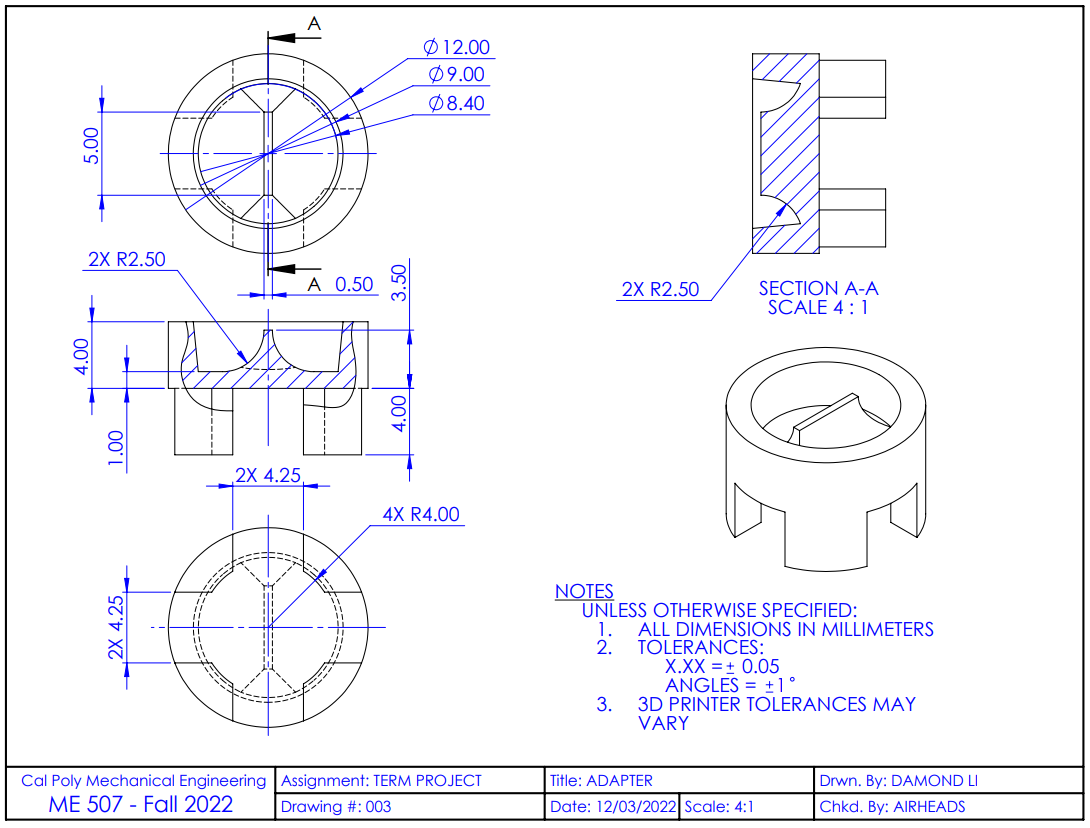
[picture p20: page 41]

41

42

## c. Model Glider Design by Josh Bixler [1]

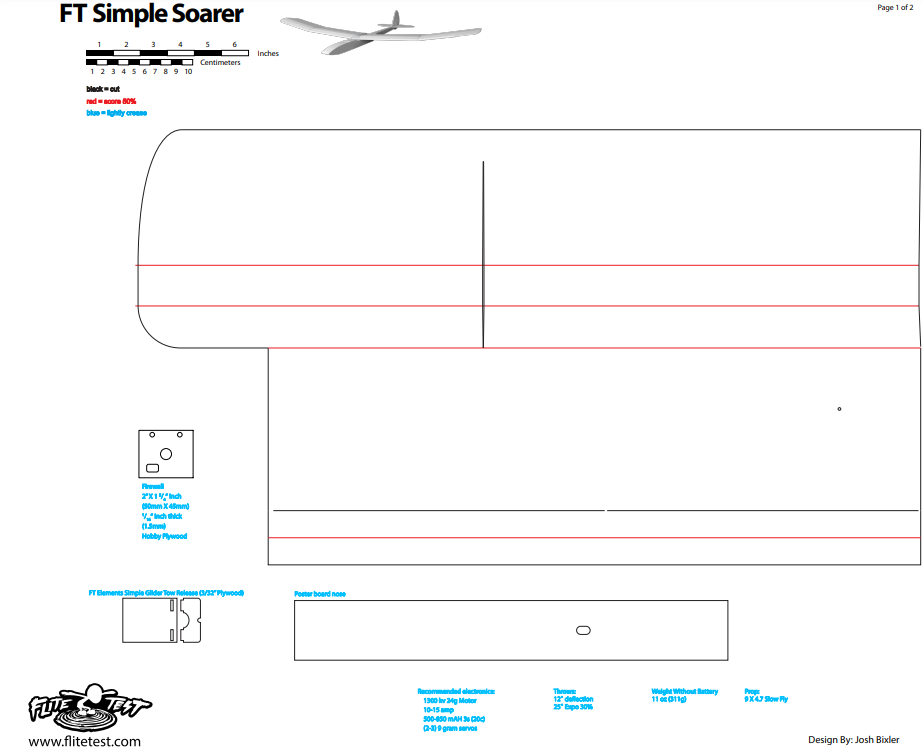
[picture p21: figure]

43

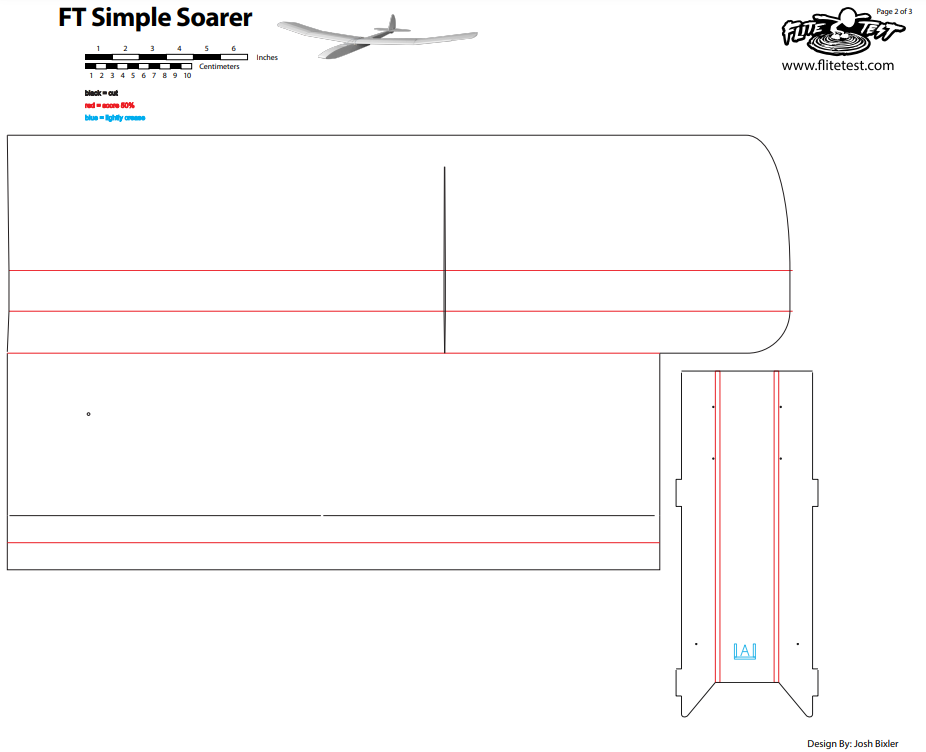
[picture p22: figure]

44

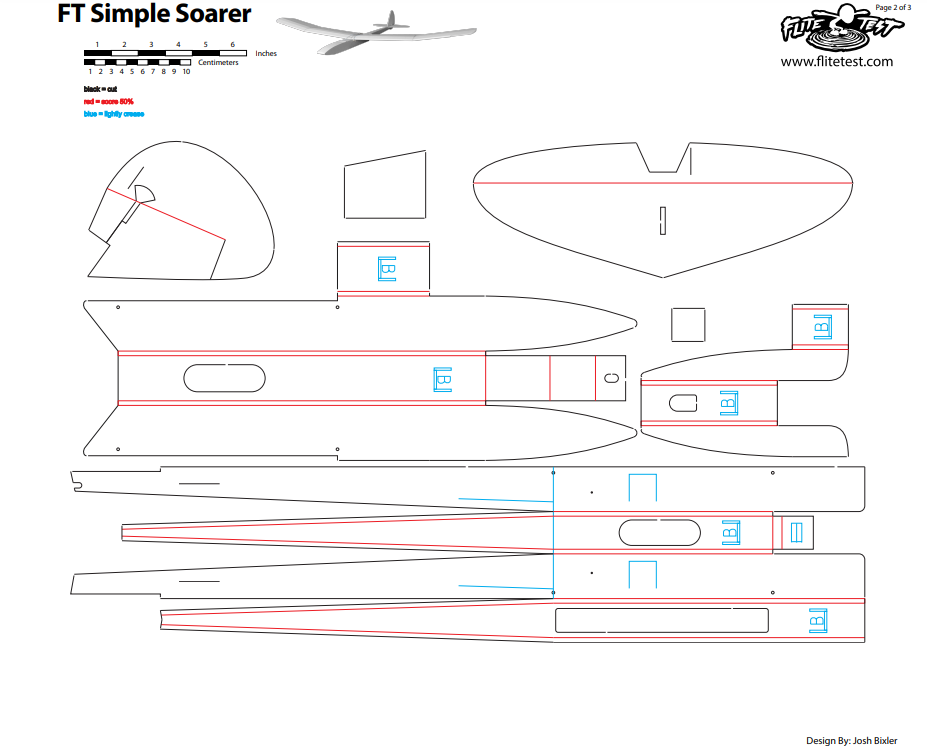
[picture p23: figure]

45

## VIII. References

[1] Bixler, John, “FT Simple Soarer”, Flite Test Store. https://store.flitetest.com/ft-simple-soarer-wr-1460mm/.
[2] De Bonet, Lucas, “How to build cheap VR Haptic Gloves to FEEL VR.”, https://www.youtube.com/watch?v=2yF-SJcg3zQ.
[3] Ridgely, John, “ME-507 Canvas Modules”, https://canvas.calpoly.edu/courses/85917.
[4] Ridgely, John, “ME 507 Support Files”, https://github.com/spluttflob/ME507-Support.
[5] Santos, Rui, “ESP32 PWM with Arduino IDE (Analog Output)”, https://randomnerdtutorials.com/esp32-pwm-arduino-ide/.

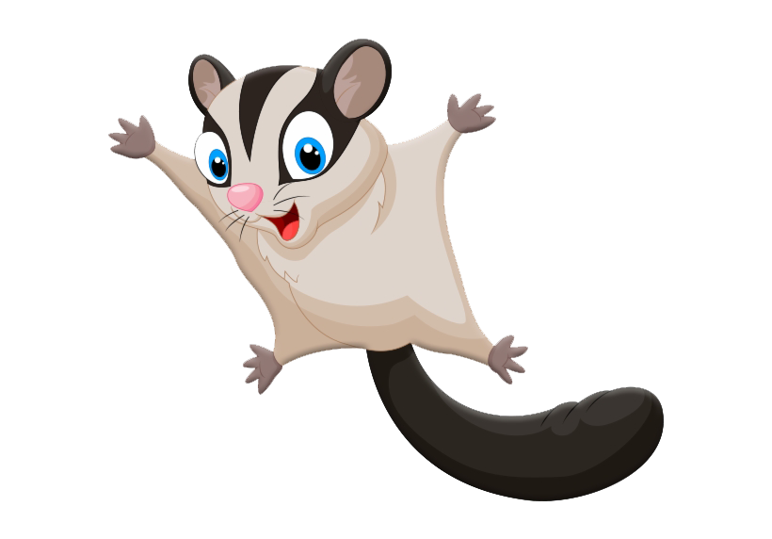
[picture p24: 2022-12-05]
docs/sugar-glider.png

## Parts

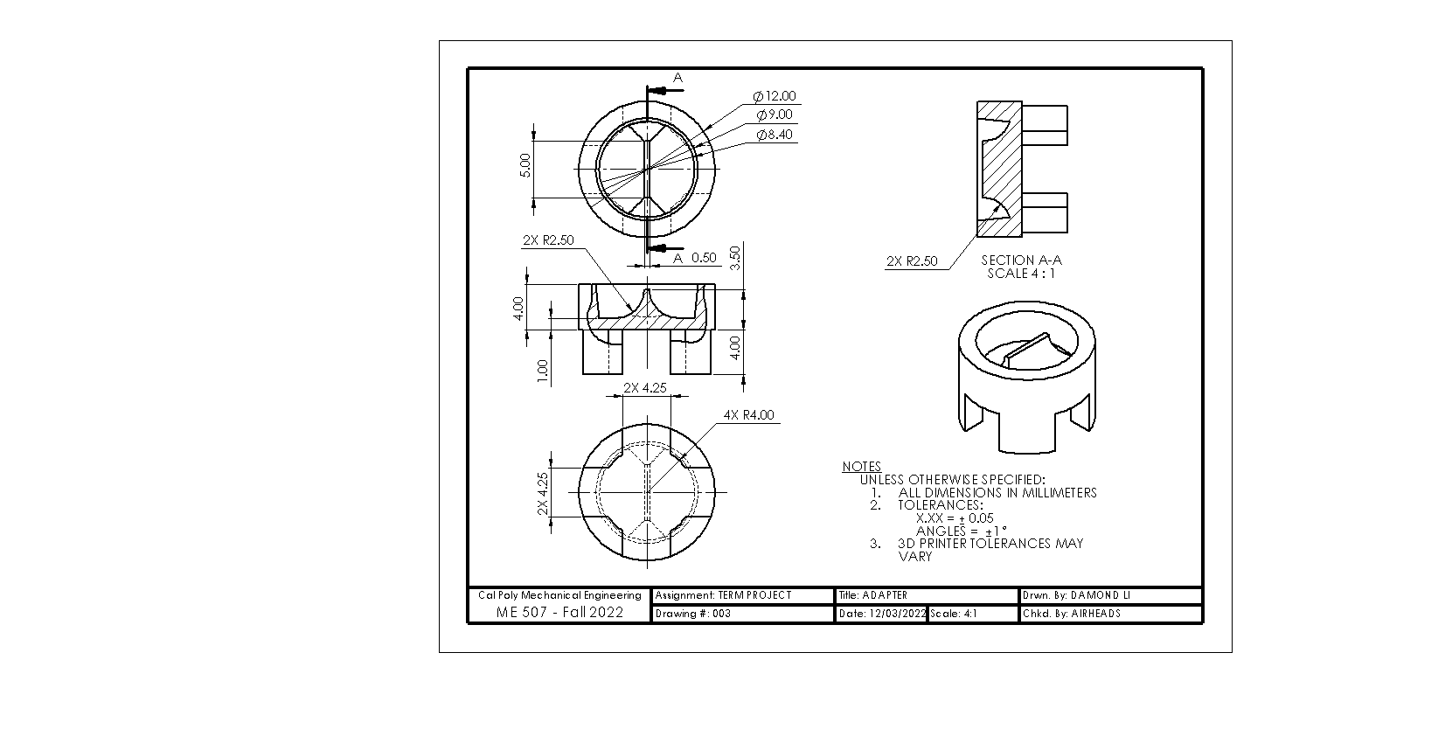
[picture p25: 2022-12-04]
SOLIDWORKS PARTS/ADAPTER DRAWING.PNG

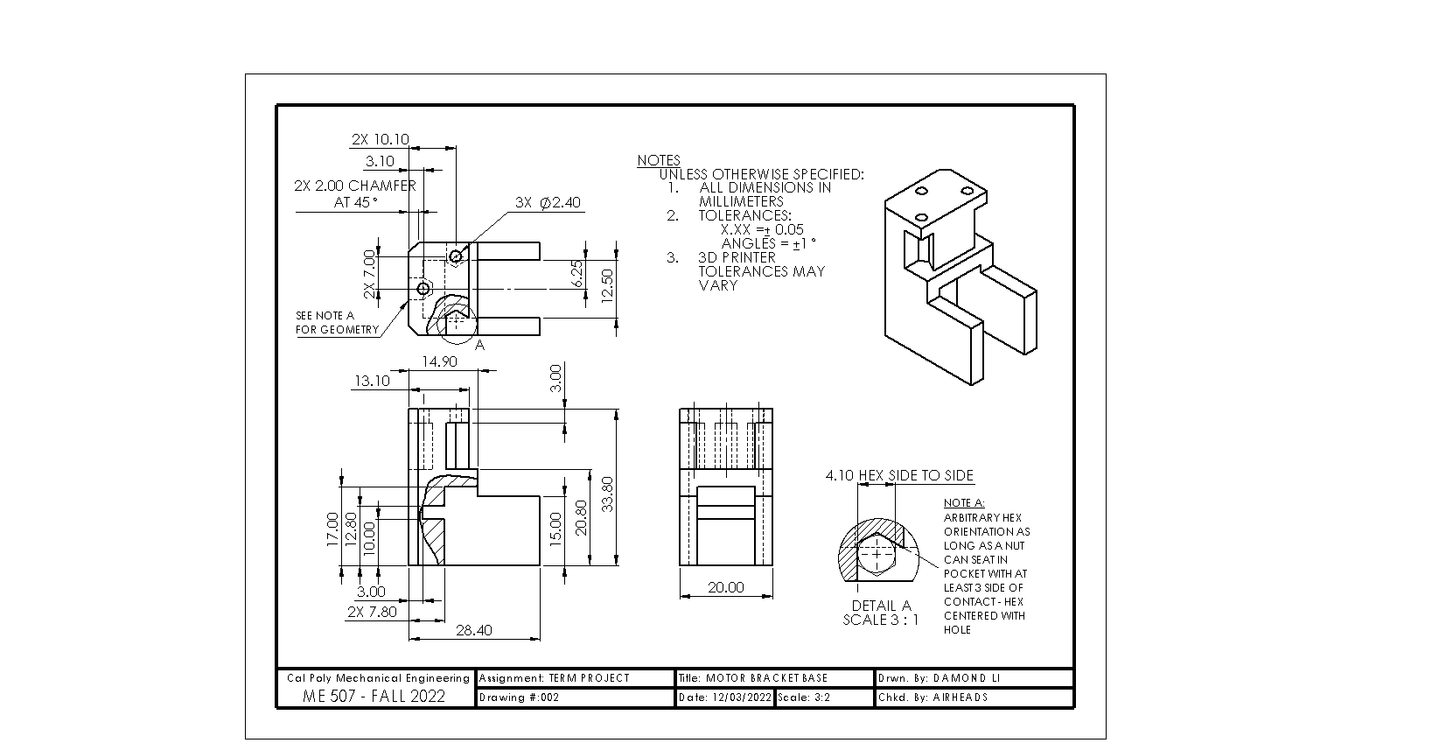
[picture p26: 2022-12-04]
SOLIDWORKS PARTS/MOTOR BRACKET BASE.PNG

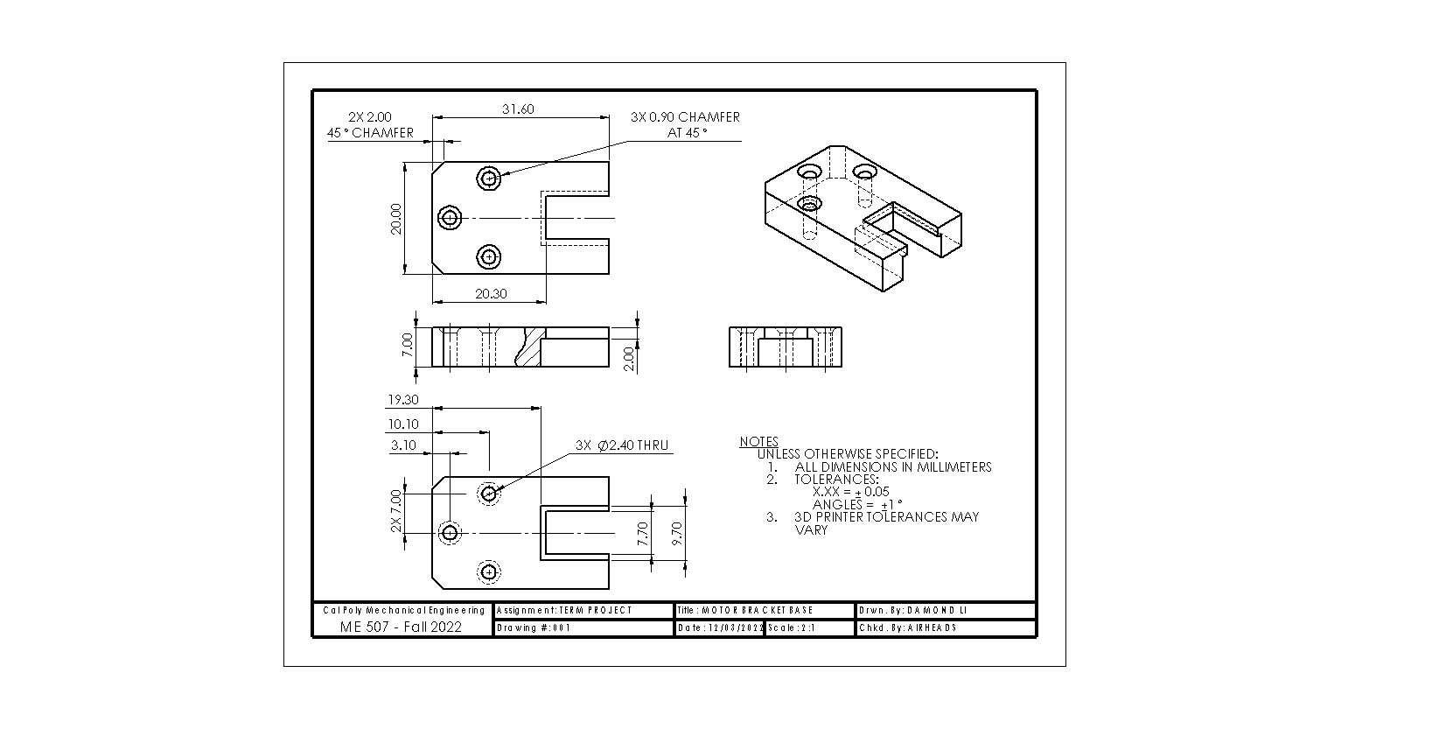
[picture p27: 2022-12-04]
SOLIDWORKS PARTS/MOTOR BRACKET CAP.PNG

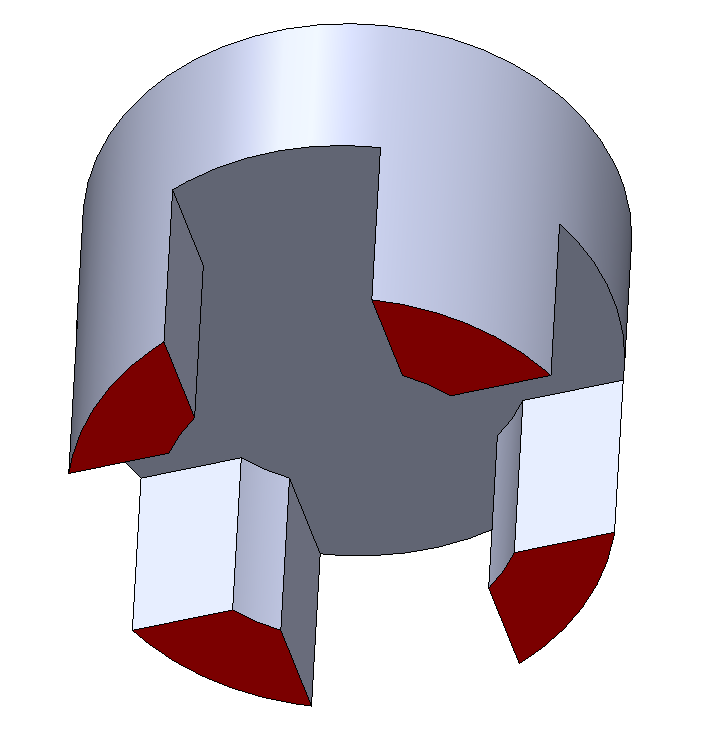
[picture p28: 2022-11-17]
SOLIDWORKS PARTS/ADAPTER.PNG

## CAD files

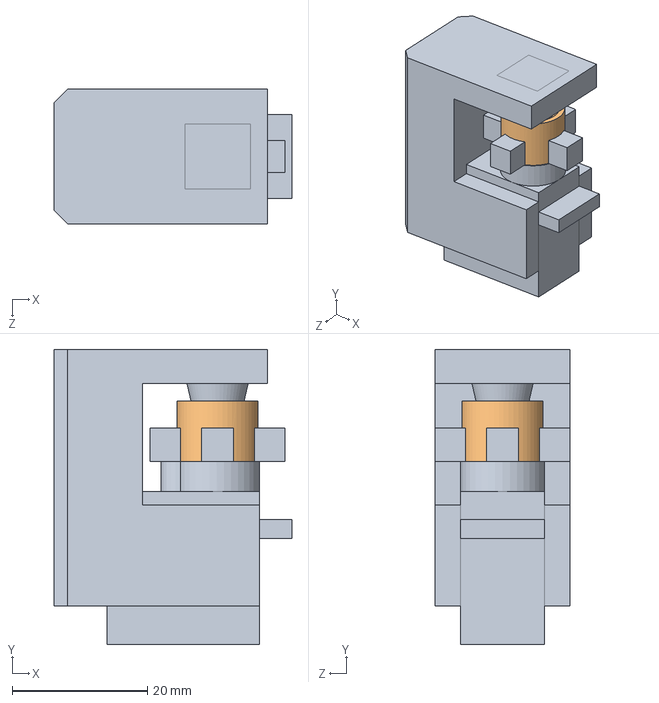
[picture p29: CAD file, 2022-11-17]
SOLIDWORKS PARTS/ASSEMBLY.SLDASM
35.2 x 43.7 x 20.0 mm
MOTOR BRACKET
ADAPTER

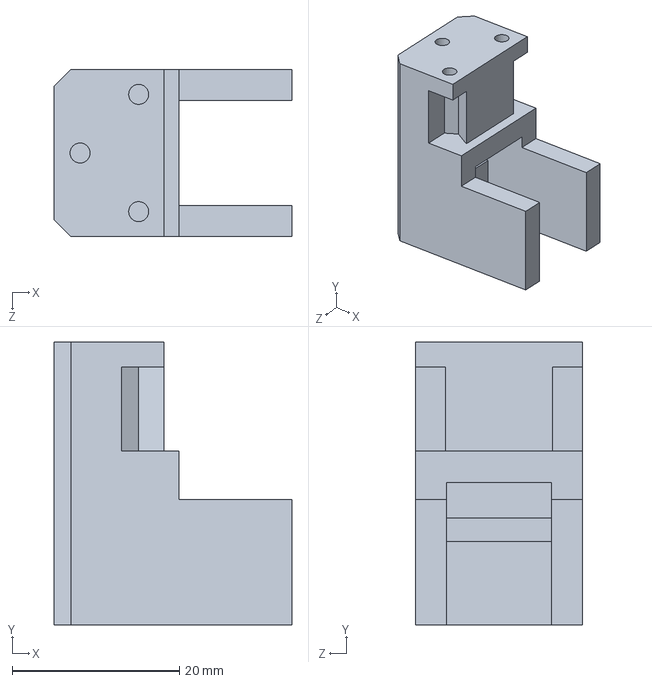
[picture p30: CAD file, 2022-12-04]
SOLIDWORKS PARTS/MOTOR BRACKET BASE.SLDPRT
28.4 x 33.8 x 20.0 mm

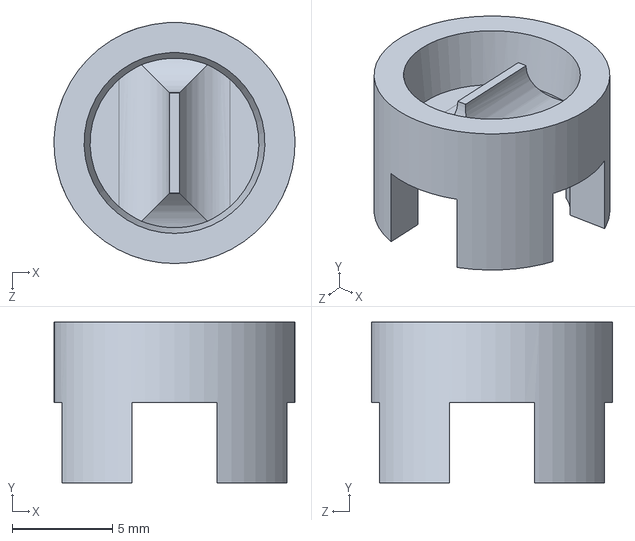
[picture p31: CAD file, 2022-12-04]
SOLIDWORKS PARTS/ADAPTER.SLDPRT
12.0 x 8.00 x 12.0 mm

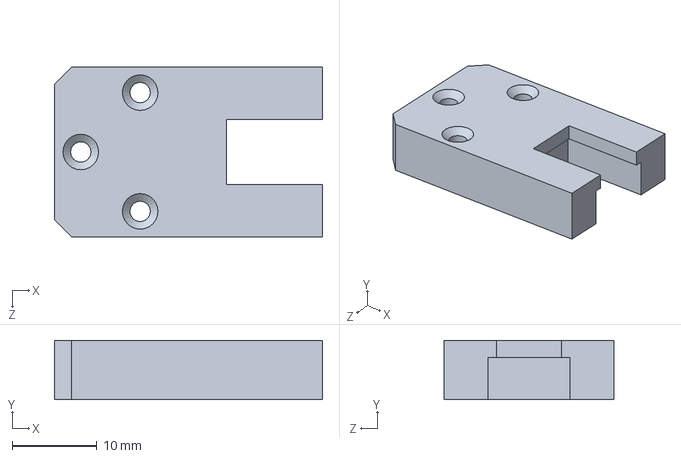
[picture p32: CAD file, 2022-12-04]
SOLIDWORKS PARTS/MOTOR BRACKET CAP.SLDPRT
31.6 x 7.00 x 20.0 mm

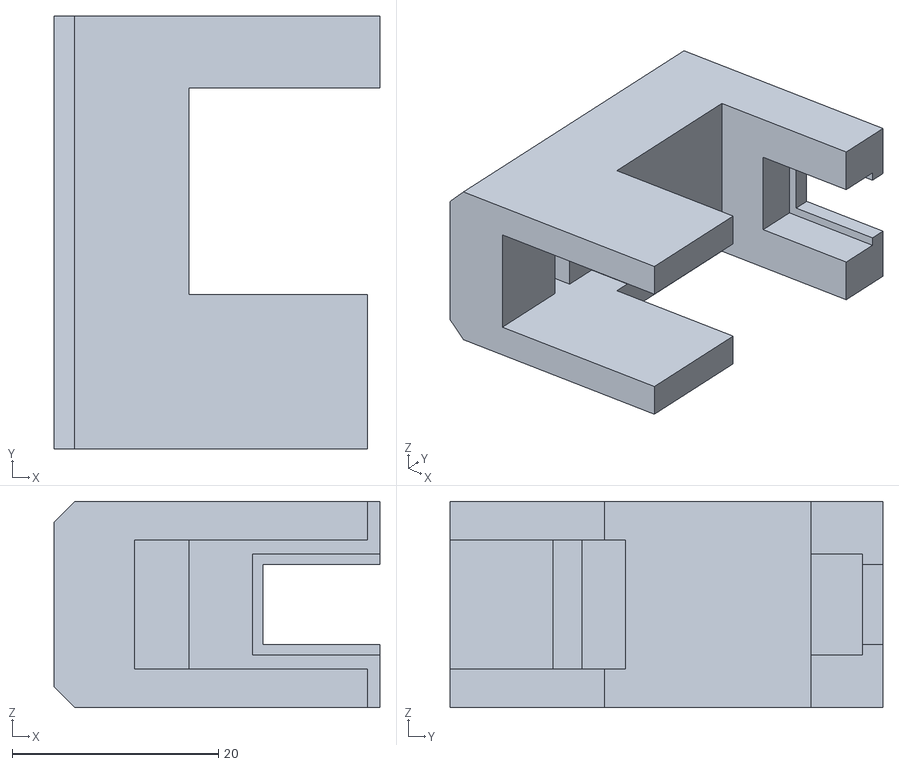
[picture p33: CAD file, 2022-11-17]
SOLIDWORKS PARTS/MOTOR BRACKET V2.STL
31.6 x 42.0 x 20.0

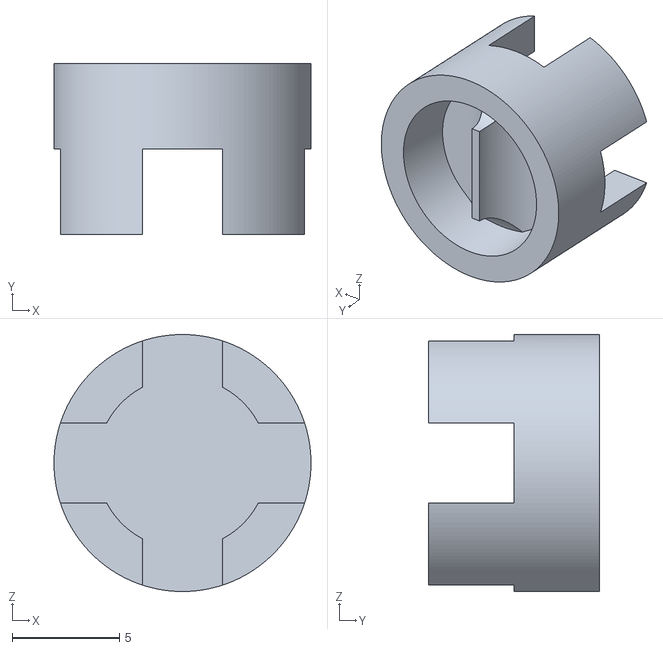
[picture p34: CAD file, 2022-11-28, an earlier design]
SOLIDWORKS PARTS/ADAPTER V2.STL
12.0 x 8.00 x 12.0

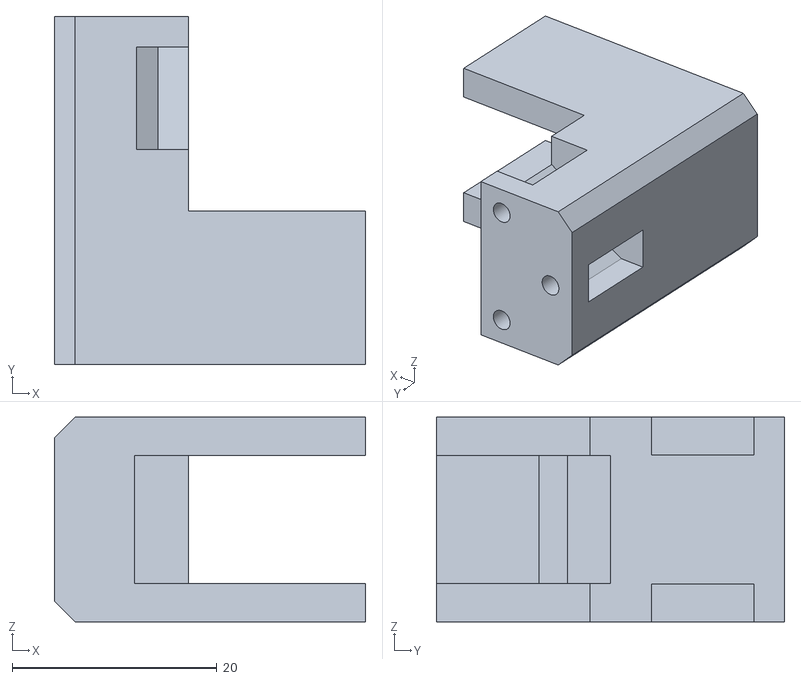
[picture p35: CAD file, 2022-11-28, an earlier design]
SOLIDWORKS PARTS/MOTOR BRACKET V3 P2.STL
30.4 x 34.0 x 20.0

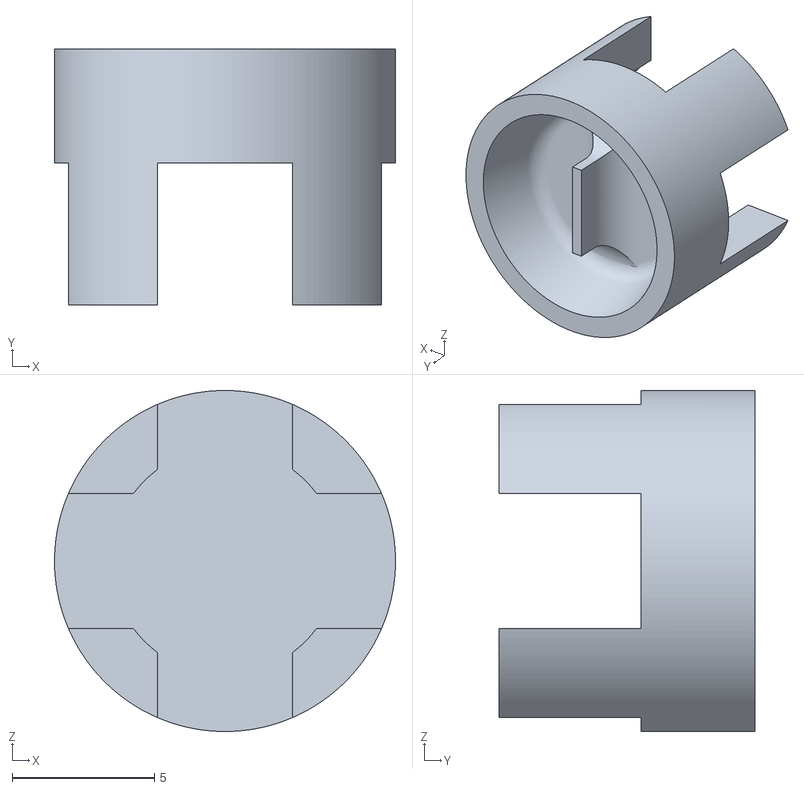
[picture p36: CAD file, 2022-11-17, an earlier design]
SOLIDWORKS PARTS/ADAPTER V1.STL
12.0 x 9.00 x 12.0

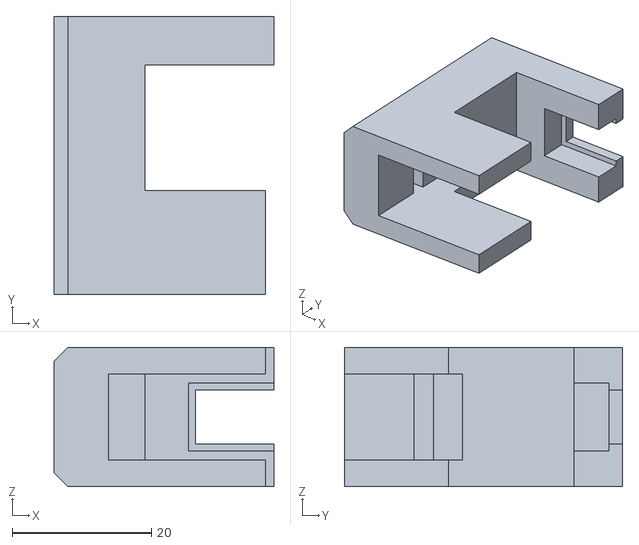
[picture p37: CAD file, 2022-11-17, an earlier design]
SOLIDWORKS PARTS/MOTOR BRACKET V1.STL
31.6 x 40.0 x 20.0

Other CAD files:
SOLIDWORKS PARTS/MOTOR BRACKET.SLDPRT
SOLIDWORKS PARTS/MOTOR BRACKET V4 P2.STL
SOLIDWORKS PARTS/ADAPTER V3.STL
SOLIDWORKS PARTS/MOTOR BRACKET V4 P1.STL
SOLIDWORKS PARTS/MOTOR BRACKET V3 P1.STL
SOLIDWORKS PARTS/ADAPTER.SLDDRW
SOLIDWORKS PARTS/MOTOR BRACKET BASE.SLDDRW
SOLIDWORKS PARTS/MOTOR BRACKET CAP.SLDDRW

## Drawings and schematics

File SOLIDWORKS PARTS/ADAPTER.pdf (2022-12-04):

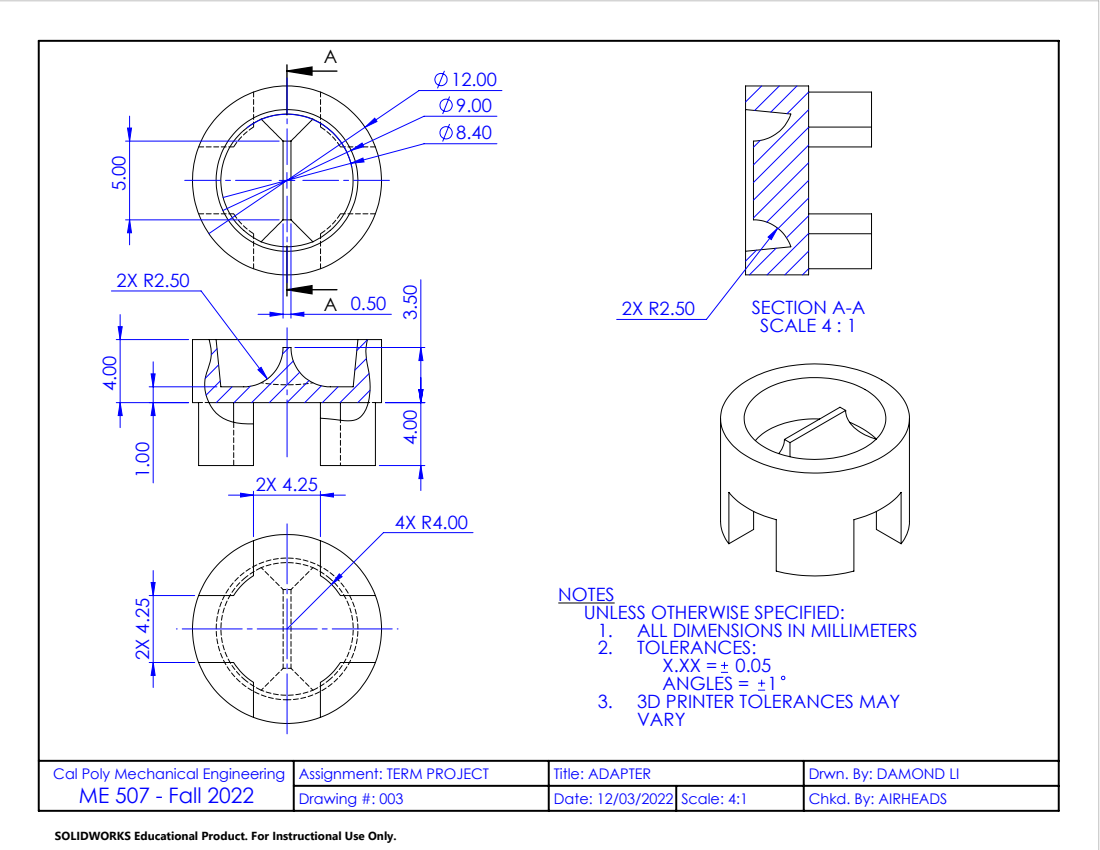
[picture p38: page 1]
SECTION A-A; SCALE 4 : 1; ANGLES =

NOTES
UNLESS OTHERWISE SPECIFIED:
1. ALL DIMENSIONS IN MILLIMETERS
2. TOLERANCES:
3. 3D PRINTER TOLERANCES MAY
VARY

Cal Poly Mechanical Engineering ME 507 - Fall 2022 | Assignment: TERM PROJECT | Title: ADAPTER | Drwn. By: DAMOND LI
Drawing #: 003 | Date: 12/03/2022 | Scale: 4:1 | Chkd. By: AIRHEADS

SOLIDWORKS Educational Product. For Instructional Use Only.

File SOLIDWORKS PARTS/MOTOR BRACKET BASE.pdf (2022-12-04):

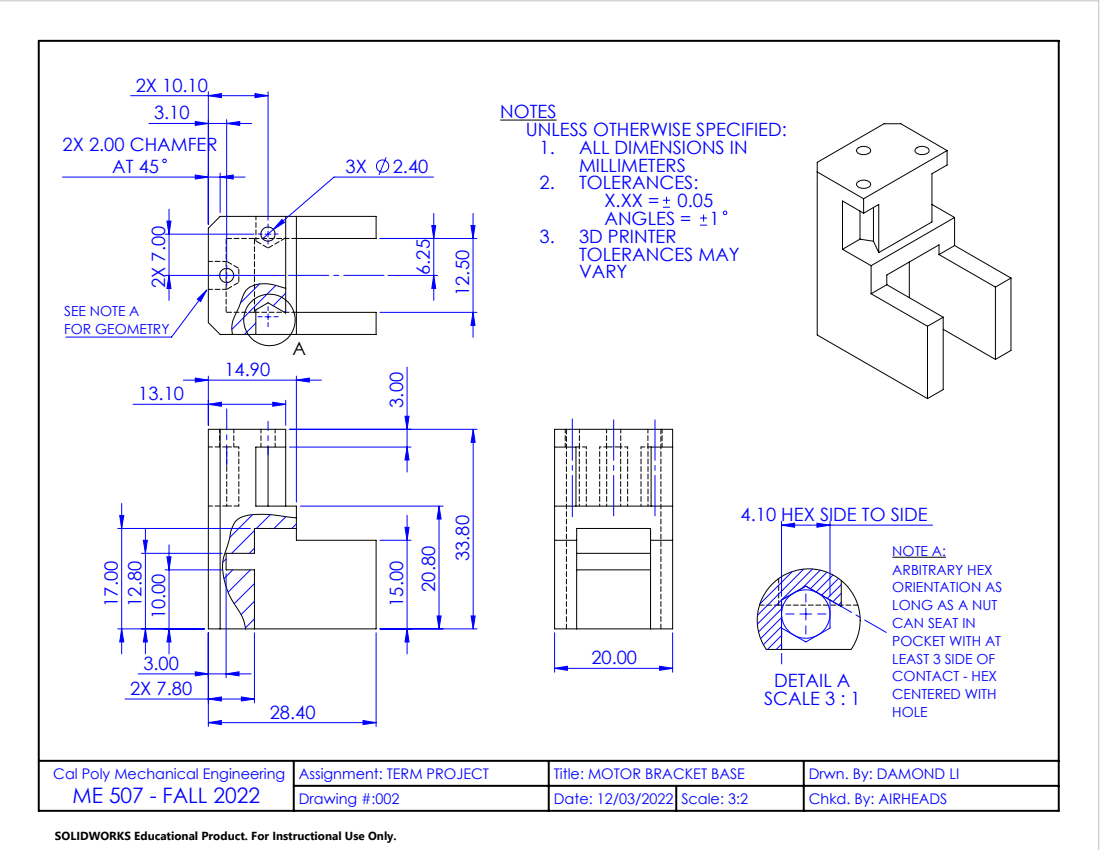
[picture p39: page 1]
2X 2.00 CHAMFER AT 45; SEE NOTE A FOR GEOMETRY; DETAIL A SCALE 3 : 1; ANGLES =

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

4.10 HEX SIDE TO SIDE

NOTE A:
ARBITRARY HEX
ORIENTATION AS
LONG AS A NUT
CAN SEAT IN
POCKET WITH AT
LEAST 3 SIDE OF
CONTACT - HEX
CENTERED WITH
HOLE

Cal Poly Mechanical Engineering ME 507 - FALL 2022 | Assignment: TERM PROJECT | Title: MOTOR BRACKET BASE | Drwn. By: DAMOND LI
Drawing #:002 | Date: 12/03/2022 | Scale: 3:2 | Chkd. By: AIRHEADS

SOLIDWORKS Educational Product. For Instructional Use Only.

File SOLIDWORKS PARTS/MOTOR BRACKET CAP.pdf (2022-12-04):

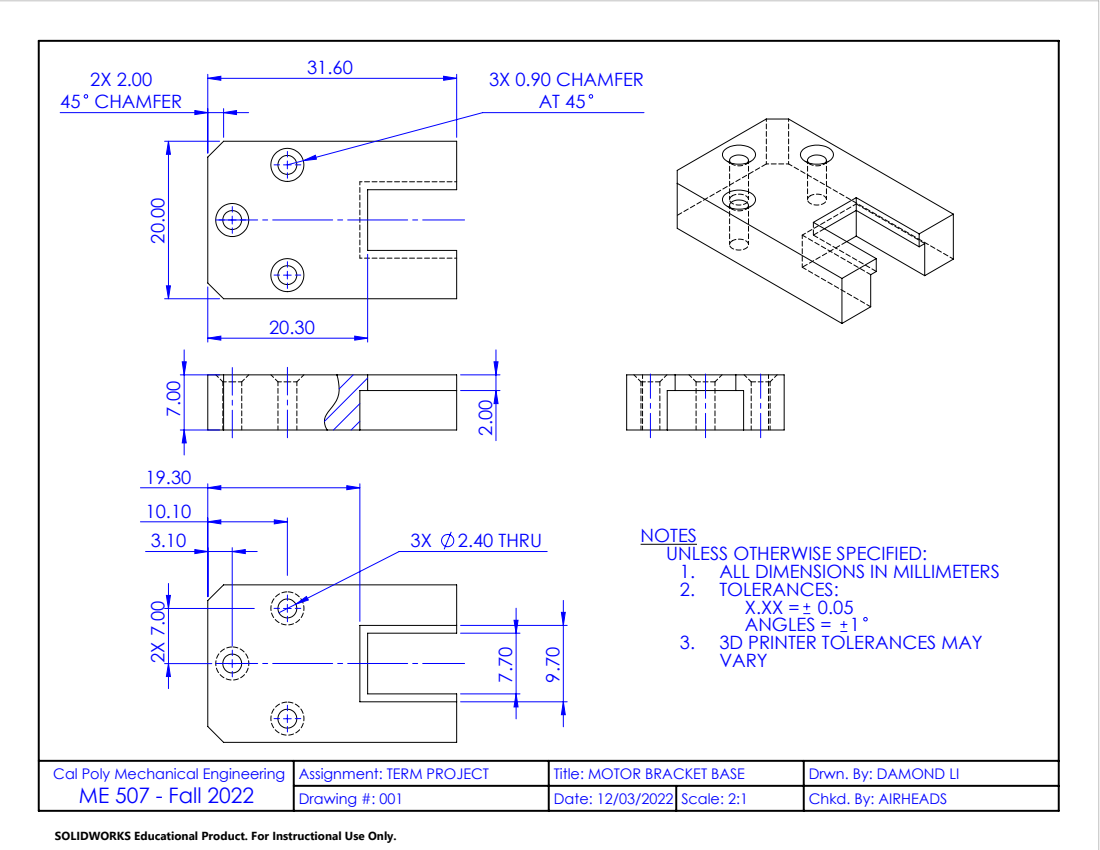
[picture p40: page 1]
2X 2.00 45 CHAMFER; 3X 0.90 CHAMFER AT 45; 3X 2.40 THRU 7.70; ANGLES =

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

Cal Poly Mechanical Engineering ME 507 - Fall 2022 | Assignment: TERM PROJECT | Title: MOTOR BRACKET BASE | Drwn. By: DAMOND LI
Drawing #: 001 | Date: 12/03/2022 | Scale: 2:1 | Chkd. By: AIRHEADS

SOLIDWORKS Educational Product. For Instructional Use Only.

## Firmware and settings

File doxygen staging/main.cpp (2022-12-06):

/** @file main.cpp
 *  @brief Main file for ME 507 Airheads project. Safely lands an unpowered model airplane.
 *  @details Includes ultrasonic sensor, potentiometer, motor driver, and flight controller tasks.
 *  @author ME 507 Airheads
 *  @date 2022-Nov-10 
 */

#include <Arduino.h>
#include "shares.h"
#include "taskshare.h"
#include "PrintStream.h"
#include <time.h>
#include <network.h>

// Modules
#include "DRV8871.h"
#include "ultrasonic.h"
#include "potentiometer.h"
#include "PIDController.h"
#include "IMU.h"

// Shares
Share<bool> near_ground ("Near Ground");                    ///< A share boolean that reads true if the glider is near ground
Share<uint8_t> tc_state ("Task Controller State");          ///< A share integer for finite state machine
Share<int16_t> rudder_duty ("Rudder motor duty cycle");     ///< A share containing the duty cycle for rudder motor
Share<int16_t> elev_duty ("Elevator motor duty cycle");     ///< A share containing the duty cycle for elevator motor
Share<float> yawC ("Current yaw from IMU");                 ///< A share containing current yaw of the glider
Share<float> pitchC ("Current pitch from IMU");             ///< A share containing current pitch of the glider

// Elevator Motor (Motor 0)
#define ELEVATOR_PIN_IN1   27       ///< GPIO 27 on ESP32: non-zero signal for (+) duty cycle
#define ELEVATOR_PIN_IN2   33       ///< GPIO 33 on ESP32: non-zero signal for (-) duty cycle
#define ELEVATOR_CHANNEL_A 2        ///< GPIO 2 on ESP32: unique channel
#define ELEVATOR_CHANNEL_B 3        ///< GPIO 3 on ESP32: unique channel

// Rudder Motor (Motor 1)
#define RUDDER_PIN_IN1   16         ///< GPIO 16 on ESP32: non-zero signal for (+) duty cycle
#define RUDDER_PIN_IN2   17         ///< GPIO 17 on ESP32: non-zero signal for (-) duty cycle
#define RUDDER_CHANNEL_A 0          ///< GPIO 0 on ESP32: unique channel
#define RUDDER_CHANNEL_B 1          ///< GPIO 1 on ESP32: unique channel

// Potentiometers
#define ELEVATOR_POT_PIN 34         ///< GPIO 34 on ESP32: reads voltage from elevator potentiometer
#define RUDDER_POT_PIN   39         ///< GPIO 39 on ESP32: reads voltage from rudder potentiometer

// Ultrasonic
#define TRIG 12                     ///< GPIO 12 on ESP32: ultrasonic trigger pin
#define ECHO 13                     ///< GPIO 1 on ESP32: ultrasonic echo pin

/** @brief   Ultrasonic sensor measures distance to the ground
 *  @details Ultrasonic sensor mounted on the airplane measures the 
 *           distance from the airplane to the ground. When the airplane
 *           is within 1 foot of the ground, the airplane's control 
 *           surfaces will move into "landing configuration" where the 
 *           pitch will be x degrees up for a soft landing.
 *  @param   p_params A pointer to parameters passed to this task. This 
 *           pointer is ignored; it should be set to @c NULL in the 
 *           call to @c xTaskCreate() which starts this task
 */
void task_ultrasonic (void* p_params)
{
    Serial << "Ultrasonic Sensor Task Begin" << endl;

    // Task period
    const uint8_t period = 100;

    // Distance
    float distance;

    // Height and timer threshold
    const uint8_t threshold = 20;               // cm

    // Create object
    Serial.println("Constructing the ultrasonic object");
    Ultrasonic ultra = Ultrasonic(ECHO, TRIG);

    while (true)
    {
        // Get the distance from the sensor
        distance = ultra.get_distance();
        
        // If the distance is below height threshold, start counting
        // Stop counting when counter exceeds 10 seconds to prevent overflow
        near_ground.put(distance < threshold);
        vTaskDelay(period);
    }
}


/** @brief   Controller for both rudder and elevator control surfaces
 *  @details Retrieves IMU, potentiometer, and ultrasonic sensor data and writes 
 *           motor duty cycles to shares. The motor tasks use the duty cycles
 *           to move the rudder and elevator control surfaces. The states within
 *           this task are set internally and by the webpage task.
 *  @param   p_params An unused pointer to (no) parameters passed to this task
 */
void task_controller (void* p_params)
{
    Serial << "Controller Task Begin" << endl;
  
    const uint8_t TASK_CONTROLLER_PERIOD = 50;  ///< Period of controller task (ms)

    // Controller objects
    PIDController yaw2rudder =      ///< Controller for rudder angle based on yaw
        PIDController(1,0,0,TASK_CONTROLLER_PERIOD); 
    PIDController rudder2duty =     ///< Controller for duty cycle based on rudder angle
        PIDController(3,0,0,TASK_CONTROLLER_PERIOD);
    PIDController pitch2elev =      ///< Controller for elevator angle based on pitch
        PIDController(1,0,0,TASK_CONTROLLER_PERIOD);
    PIDController elev2duty =       ///< Controller for duty cycle based on elevator angle
        PIDController(3,0,0,TASK_CONTROLLER_PERIOD);

    // Create potentiometer object and zero the current reading
    Potentiometer rudderPot = Potentiometer(RUDDER_POT_PIN, 0);
    rudderPot.zero();

    // Create potentiometer object and zero the current reading
    Potentiometer elevPot = Potentiometer(ELEVATOR_POT_PIN, 0);
    elevPot.zero();

    // Initialize variables
    float yawD;                     ///< Desired yaw (deg)
    float pitchD;                   ///< Desired pitch (deg)  

    // Variables to keep track of previous potentiometer reading
    float prev_rudder = 0;          ///< Rudder position at previous time (deg)
    float prev_elevator = 0;        ///< Elevator position at previous time (deg)

    float rudderAngleD;             ///< Desired rudder angle (deg)
    float rudderAngleC;             ///< Current rudder angle (deg)
    float rudderAngleMin = -50;     ///< Minimum allowable rudder angle (deg)
    float rudderAngleMax = 50;      ///< Maximum allowable rudder angle (deg)

    float elevAngleD;               ///< Desired elevator angle (deg)
    float elevAngleC;               ///< Current elevator angle (deg)
    float elevAngleMin = -50;       ///< Minimum allowable elevator angle (deg)
    float elevAngleMax = 50;        ///< Maximum allowable elevator angle (deg)

    float rudderDutyD;              ///< Rudder motor duty cycle (-100% to 100% incl.)
    float elevDutyD;                ///< Elev motor duty cycle (-100% to 100% incl.)

    uint16_t delay_time = 0;        ///< Current amount of time (ms) in inactive delay
    tc_state.put(0);                // Initialize at state 0


    // Establish initial conditions for rudder and elevator
    rudderAngleC = rudderPot.get_angle();
    prev_rudder = rudderAngleC;

    elevAngleC = elevPot.get_angle();
    prev_elevator = elevAngleC;

    
    while (true) 
    {

        if (web_calibrate.get()) {        // If the webpage calls for calibration

            rudderPot.zero();             // Stop power to motors
            elevPot.zero();

            web_calibrate.put(0);         // Reset the calibrate flag

            Serial << "   Calibrated" << endl;

        }


        if (tc_state.get() == 0)          // STATE 0: DISABLED
        {        

            delay_time = 0;               // Reset delay counter
            rudder_duty.put(0);           // Stop power to motors
            elev_duty.put(0);

            // Passive state waiting for external callback to switch state
            Serial.println(" 0 ");

        }
        else if (tc_state.get() == 1)     // STATE 1: WAIT FOR LAUNCH
        {

            Serial.println(" 1 ");

            // Add one task period to accumulated delay time (ms)
            if (near_ground.get() == 0) 
            {
                delay_time += TASK_CONTROLLER_PERIOD;         
            }  
            else
            {
                delay_time = 0;
            }

            // If total delay time has reached 1000 ms...
            if (delay_time >= 2000) 
            {

                tc_state.put(2);                // Move to active state
                delay_time = 0;                 // Reset counter
            }

        }
        else if (tc_state.get() == 2)           // STATE 2: CONTROLLER ACTIVE
        {

            // Time how long the plane is near the ground
            if (near_ground.get() == 1) 
            {
                delay_time += TASK_CONTROLLER_PERIOD;         
            }  
            else
            {
                delay_time = 0;
            }

            // If total delay time has reached 2000 ms...
            if (delay_time >= 2000) 
            {
                tc_state.put(0);                // Move to deactivated state
                delay_time = 0;                 // Reset counter
            }

            // Check whether the glider is near ground
            if (near_ground.get()) 
            {
                pitchD = 10;                    // If it is, set pitch
            }
            else 
            {
                pitchD = 0;                     // If not, set different pitch
            }

            yawD = 0;          
        
            // Calculate desired rudder angle and then saturate
            rudderAngleD = yaw2rudder.getCtrlOutput(yawC.get(),yawD);
            if (rudderAngleD > rudderAngleMax) 
            {
                rudderAngleD = rudderAngleMax;
            }
            else if (rudderAngleD < rudderAngleMin) 
            {
                rudderAngleD = rudderAngleMin;
            }

            // Get current rudder angle
            rudderAngleC = rudderPot.get_angle();
            // Check if the difference in rudder angles are less than 30 degrees
            // to prevent undesired response to flickering measurements
            if (fabs(rudderAngleC - prev_rudder) < 30)
            {
                // Serial.println(fabs(rudderAngleC - prev_rudder));
                prev_rudder = rudderAngleC;
                // Calculate desired rudder motor duty cycle, saturate, then put to share
                rudderDutyD = rudder2duty.getCtrlOutput(rudderAngleC,rudderAngleD);
                if (rudderDutyD > 100) 
                {
                    rudder_duty.put(100);
                }
                else if (rudderDutyD < -100) 
                {
                    rudder_duty.put(-100);
                }
                else
                {
                    rudder_duty.put((int16_t) round(rudderDutyD));
                }
            }
            else
            {
                rudder_duty.put(0);
            }
            

            // Calculate desired elevator angle and then saturate
            elevAngleD = pitch2elev.getCtrlOutput(pitchC.get(),pitchD);
            if (elevAngleD > elevAngleMax)
            {
                elevAngleD = elevAngleMax;
            }
            else if (elevAngleD < elevAngleMin)
            {
                elevAngleD = elevAngleMin;
            }

            // Get current elevator angle
            elevAngleC = elevPot.get_angle();
            if (fabs(elevAngleC - prev_elevator) < 30)
            {
                // Calculate desired elevator motor duty cycle, saturate, then put to share
                elevDutyD = elev2duty.getCtrlOutput(elevAngleC,elevAngleD);
                if (elevDutyD > 100) 
                {
                    elev_duty.put(100);
                }
                else if (elevDutyD < -100) 
                {
                    elev_duty.put(-100);
                }
                else 
                {
                    elev_duty.put((int16_t) round(elevDutyD));
                }
            }
            else
            {
                elev_duty.put(0);
            }

            Serial << "C: " << elevAngleC << "; D: " << elevAngleD << "; Duty: " << elev_duty.get() << endl;

            prev_elevator = elevAngleC;
            prev_rudder = rudderAngleC;

        }

        vTaskDelay(TASK_CONTROLLER_PERIOD);

    }
}

/** @brief   
 *  @details 
 *  @param   p_params A pointer to parameters passed to this task. This 
 *           pointer is ignored; it should be set to @c NULL in the 
 *           call to @c xTaskCreate() which starts this task
 */
void task_rudder_motor (void* p_params)
{ 

    // Motor task period
    const uint8_t period = 50;

    Serial << "Rudder Motor Task Begin" << endl;
    // Create object
    DRV8871 rudder = DRV8871(RUDDER_PIN_IN1, RUDDER_PIN_IN2, RUDDER_CHANNEL_A, RUDDER_CHANNEL_B);

    rudder.set_duty(0);

    while (true)
    {
        // Serial.println(rudder_duty.get());
        rudder.set_duty(rudder_duty.get());
        vTaskDelay(period);
    }
}   

/** @brief   
 *  @details 
 *  @param   p_params A pointer to parameters passed to this task. This 
 *           pointer is ignored; it should be set to @c NULL in the 
 *           call to @c xTaskCreate() which starts this task
 */
void task_elevator_motor (void* p_params)
{
    
    // Motor task period
    const uint8_t period = 50;

    Serial << "Elevator Motor Task Begin" << endl;
    // Create object
    DRV8871 elevator = DRV8871(
        ELEVATOR_PIN_IN1, ELEVATOR_PIN_IN2, ELEVATOR_CHANNEL_A, ELEVATOR_CHANNEL_B);

    elevator.set_duty(0);

    while (true)
    {
      elevator.set_duty(elev_duty.get());
      vTaskDelay(period);
    }
}

/** @brief   Task function to interface with IMU
 *  @details This task reads from the IMU to get pitch, yaw, and roll
 *           measurements. It then puts the data into shaes for the 
 *           controller to use. 
 *  @param   p_params A pointer to parameters passed to this task. This 
 *           pointer is ignored; it should be set to @c NULL in the 
 *           call to @c xTaskCreate() which starts this task
 */
void task_IMU(void* p_params) 
{
    // INIT
    LSM6DSOX imu;
    // declare float
    float pitch, yaw, roll;

    // READ VALUES
    while(true)
    {

        // SEND IT AND THE DATA BACK IN RADIANS
        imu.get_angle((float)time(0), pitch, yaw, roll);

        // Serial << "P: " << pitch*180/M_PI << ";  R: " << roll*180/M_PI << endl;

        // PUT ANGLES TO SHARES FOR CONTROLLER
        pitchC.put(pitch*180/M_PI);
        yawC.put(roll*180/M_PI);

        // PRINT IT
        // Serial << pitch * 180/M_PI << ", " << yaw * 180/M_PI << ", " << roll * 180/M_PI << endl;
        
        vTaskDelay(1);
    }
}


/** @brief   The Arduino setup function.
 *  @details This function is used to set up the microcontroller by starting
 *           the serial port and creating the tasks.
 */
void setup (void) 
{
    // The serial port must begin before it may be used
    Serial.begin (115200);

    // Wait for serial to finish setting up before proceeding
    while (!Serial) 
    {
    }

    Serial << "Serial is ready. " << endl;

    // start i2c
    Wire.begin();

    // Setup webpage
    setup_wifi();

    // Initialize web_calibrate to zero
    web_calibrate.put(1);

    // Task which runs the web server. It runs at a low priority
    xTaskCreate (task_webserver, "Web Server", 8192, NULL, 10, NULL);

    // Task for the potentiometer testing
    xTaskCreate (task_rudder_motor, "Rudder Motor", 2048, NULL, 20, NULL);

    // Task for the potentiometer testing
    xTaskCreate (task_elevator_motor, "Elevator Motor", 2048, NULL, 40, NULL);
    
    // Task for the ultrasonic sensor
    xTaskCreate (task_ultrasonic, "Ultrasonic Sensor", 2048, NULL, 50, NULL);

    // Task for the flight surface controls (rudder and elevator)
    xTaskCreate (task_controller, "Flight Controls", 2048,  NULL, 60, NULL);

    // Task for the IMU readings
    xTaskCreate (task_IMU, "IMU", 2048, NULL, 30, NULL);
}


/** @brief   The Arduino loop function.
 *  @details This function is called periodically by the Arduino system. It
 *           runs as a low priority task. On some microcontrollers it will
 *           crash when FreeRTOS is running, so we usually don't use this
 *           function for anything. 
 */
void loop (void)
{
}

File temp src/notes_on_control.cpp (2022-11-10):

/*

OLD. SEE WORD DOCUMENT.

We probably do not need a PID or similar controller on the
elevators or rudder, since there is high friction. We can 
direct the motor to turn until it reaches the desired position.

The PID controller will apply to the angle of the plane.
The control output will be the position of the elevator or
rudder.

Because we are controlling both pitch and yaw, this is a 
two-dimensional control system. We will first assume that
the two are independent.

The Python code for ME 418 PI controller of one motor has

MOTOR MODULE
    @class MotorDriver
        Attributes: MotorA, MotorB (both of class Motor)
    @class Motor
        Methods: 
            Set voltage percent
            Enable
            Disable

ENCODER MODULE
    @class Encoder
        Methods:
            Update
            Get position
            Set position
            Zero
            Get velocity
            Counts to rad
            Get position rad
            Get velocity rad

CONTROLLER MODULE
    @class PIController
        Methods:
            Set gains
            Run (once)
            Get PI components



Editing this for our purposes, we have

DRV8871
    @class DRV8871
        Methods:
            Set duty
            Enable
            Disable
    Objects: MotorE, MotorR

POTENTIOMETER
    @class Pot
        Methods:
            Zero
            Get angle (returns rad)
            Set angle (receives rad)
    Objects: PotE, PotR

CONTROLLER
    @class Controller
        Methods:
            Set gains
            Calculate (once)
    Objects: ControllerE, ControllerR

IMU
    @class IMU
        Methods:
            Get angles
            Get angular velocities
    Objects: planeIMU

ULTRASONIC
    @class Ultrasonic
        Methods:
            Get distance
    Objects: planeUSS



*/

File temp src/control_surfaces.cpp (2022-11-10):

/** @file control_surfaces.cpp
 * This file provides angle control for the rudder and elevator
 * of a model airplane. This file controls two DC motors in 
 * microservo bodies that move the rudder and elevator control
 * surfaces. 
 * 
 *  @author ME 507 Airheads
 *  @date   2022-Nov-09
 */

#include <Arduino.h>
#include "PIDController.h"

int analogInPin = A0;
int sensorValue = 0;
int outputValue = 0;
int transistorPin = 3;

int danger_pitch = 61; // dangerous pitch angle

/** @brief Check control surface angles from IMU and calculate
 *          the desired rudder and elevator angles. 
 */
/** @brief   Task which moves the rudder of a model airplane.
 *  @details This task moves a DC motor in microservo body which
 *             moves the rudder of a model airplane, changing
 *              the airplane's yaw during flight.
 *  @param   p_params 
 */
float PIDController::setRudderAngle() 
{
    // Inputs: actual yaw from getCtrlSurfAngle(), desired yaw
    // Outputs: desired rudder angle
    // If (Actual Yaw) is left from (Desired Yaw), set (Desired Rudder Angle) to the right 
    // If (Actual Yaw) is right from (Desired Yaw), set (Desired Rudder Angle) to the left
}

/** @brief Check control surface angles from IMU and calculate
 *          the desired rudder and elevator angles. 
 */
/** @brief   Task which moves the rudder of a model airplane.
 *  @details This task moves a DC motor in microservo body which
 *             moves the rudder of a model airplane, changing
 *              the airplane's yaw during flight.
 *  @param   p_params 
 */
float PIDController::setElevatorAngle() 
{
    // Inputs: actual pitch from getCtrlSurfAngle(), desired pitch, speed, desired  speed
    // Outputs: desired elevator angle
    // If (Actual Pitch) is above (upper limit), set (Desired Elevator Angle) down  
    // If (Actual Pitch) is below (lower limit), set (Desired Elevator Angle) up
        // If (Actual Pitch) is above (Desired Pitch), set (Desired Elevator Angle) down
        // 
}

void task_elevator (void* p_params)
{
    for (;;)
    {
        
        vTaskDelay(10); // runs every 10 ms
    }
}

/** @brief   Task which moves the rudder of a model airplane.
 *  @details This task moves a DC motor in microservo body which
 *             moves the rudder of a model airplane, changing
 *              the airplane's yaw during flight.
 *  @param   p_params 
 */
void task_rudder (void* p_params)
{
    for (;;)
    {
        
        vTaskDelay(10); // runs every 10 ms
    }
}

/** @brief   The Arduino setup function.
 *  @details This function is used to set up the microcontroller by starting
 *           the serial port and creating the assigned tasks.
 */
void setup()
{
    Serial.begin (115200); // The serial port must begin before it may be used

}

/** @brief   The Arduino loop function. Empty for this assignment.
 *  @details This function is called periodically by the Arduino system. It
 *           runs as a low priority task. On some microcontrollers it will
 *           crash when FreeRTOS is running, so we usually don't use this
 *           function for anything, instead just having it delay itself. 
 */
void loop() 
{
sensorValue = analogRead(analogInPin)/4;
outputValue = map(sensorValue, 0, 1023, 0, 255);
analogWrite(transistorPin, sensorValue);

    if (sensorValue >= 160)
    {
        digitalWrite(8, HIGH);
        digitalWrite(9, LOW);
    }

    else
    { 
        
    }

    delay(10);   

 }
 

//References 
// https://learn.parallax.com/tutorials/robot/shield-bot/robotics-board-education-shield-arduino/chapter-2-shield-lights-servo-14
//https://create.arduino.cc/projecthub/RiddledExistence/controlling-a-servo-motor-with-thumb-joystick-46a4d3
//https://circuitdigest.com/microcontroller-projects/dc-motor-speed-control-using-arduino-and-potentiometer
//https://www.instructables.com/Arduino-DC-motor-speed-control-potentiometer/

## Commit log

2022-10-13 Revert "Put pleasedontcrash.cpp contents in main"
    This reverts commit 5289ce8366ac5598038ed59f7b7f0f4c9139e7be.
    [main.cpp]
2022-10-13 Fixed Build Error when trying to build ultrasonic.cpp
    removed void setup from main.cpp
    [main.cpp, ultrasonic.cpp]
2022-10-27 Added DRV8871 Motor Driver Module
2022-10-27 Motor Driver Dont Work
2022-11-03 creating header file for ultrasonic sensor task
2022-11-03 Motor Driver fixed
2022-11-04 Motor Driver Update
    [MOTOR BRACKET.SLDPRT]
2022-11-04 Potentiometer + Motor Control
    Wrote the potentiometer .cpp and .h files.
    Added motor controller to PIDController.cpp/.h
2022-11-17 Updated Solidworks Parts
    [ADAPTER V1.STL, ADAPTER.SLDPRT, ASSEMBLY.SLDASM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]
2022-11-28 Updated Solidworks files
    [ADAPTER V2.STL, ADAPTER V3.STL, ADAPTER.SLDPRT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]
2022-11-30 updated class files for imu
2022-11-30 example use case for IMU class
2022-11-30 Pots, ultrasonic, controller states working
2022-12-02 Commented on motor driver, network, potentiometer, shares, and ultrasonic
2022-12-02 Gave credit to Rui and Sara Santos for ESP32 PWM usage
2022-12-04 Comments + Solidworks drawings
    [ADAPTER.SLDDRW, ADAPTER.SLDPRT, MOTOR BRACKET BASE.SLDDRW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]
2022-12-04 Fixed small error in comment
    [main.cpp]
2022-12-06 Commented IMU files
2022-12-06 added comments for IMU task
